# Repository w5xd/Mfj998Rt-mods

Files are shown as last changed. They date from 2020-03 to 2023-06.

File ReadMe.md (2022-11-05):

<h1>MFJ998 tuner modifications.</h1>

Read <a href="LICENSE">LICENSE</a>.

Applying this modification <i><b>CAN</b></i> and <i><b>WILL</b></i> void the
manufacturer's warranty. It introduces risks to itself and your antenna and transmitter beyond those in the manufacturer's
firmware. Use of this PCB and sketch <i><b>CAN</b></i> and <i><b>WILL</b></i> 
damage any and all of these:
<ul>
<li>The MFJ998 tuner itself and components in it.
<li>Any coax cables connected to this tuner's input and/or outputs.
<li>Any antennas connected via those cables.
<li>Any transmitting and/or amplifier equipment connected to those cables.
</ul>

<h2>The Story</h2>
This project's origins can be traced back a couple years when lightning 
rendered my MFJ998RT inoperative, taking me off of 160 meters. I have lots
of experience with lightning damaging my equipment and I know its almost aways
a waste of time to try to repair it. I ordered a replacement tuner and put the dead 
one on my work bench. Eventually I took off the cover. And it occurred to me
that all the "big" parts, the relays, the inductors and capacitors, were 
probably not damaged by lighting. MFJ publishes the circuit diagram on their
website, so I started out by noticing the 5V regulator had exploded and went
from there. 
After many months
of working on it part time, I replaced one more IC (the main PIC18 uProc was the last one) and
it came up! Its as good as new. Here is the pile of dead semiconductors that
came off the lightning-struck board.
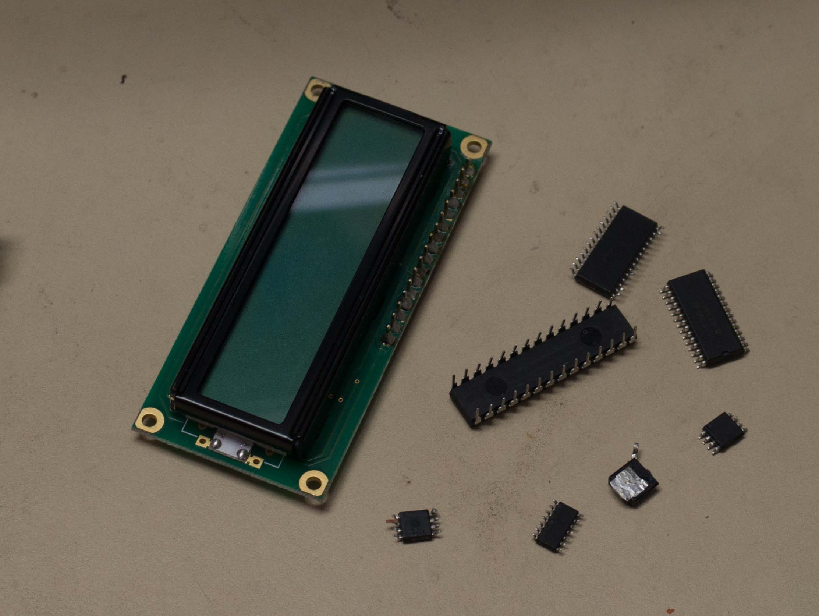
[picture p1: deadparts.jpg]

Now that I know something about how the tuner works, maybe I can improve it for my own
use?

<p>Why replace the as-designed PIC microprocessor?</p>

In contesting scenarios, I found I could not always get the MFJ998RT
to quickly tune to match at the frequency I wanted, and having to
put a low power signal to it to force the tune causes QRM
and takes time. This project adds a <a href='https://learn.sparkfun.com/tutorials/rfm69hcw-hookup-guide'>RFM69HCW 915MHz Wireless Transceiver</a> 
with a maximum range of 500m. It allows direct telemetry of the
tuner's state in both directions from the main operating shack. The
tuner, for example, can be commanded to set itself to an operating
frequency without sending any RF down its coax.

<p>Design rationale</p>

I chose the Arduino for the daughterboard because it is
inexpensive, I am familiar with the development environment, and
its pinout is more than enough to replace all the necessary
functions for the remote version of the tuner. 

<h2>Installation</h2>
<ol>
<li>Remove the weatherproof cover. 
<li>Remove the shield that covers the PIC18 uProc.
That shield has three #6 machine screws, each with a locknut, three #4 machine screws,
each with a locknut, and a #6 nut.
<li>Carefully pry the 28 pin PIC18 IC out of its socket. This is a "no holes" modification, so save the IC and you can restore factory operation by replacing it.
<li>Install this daughterboard as shown in the photo. Caution: it is possible to be
off-by-one row when pressing the daughterboard's header into the 28 pin socket. 
Use a flashlight and peer underneath before you apply power! 
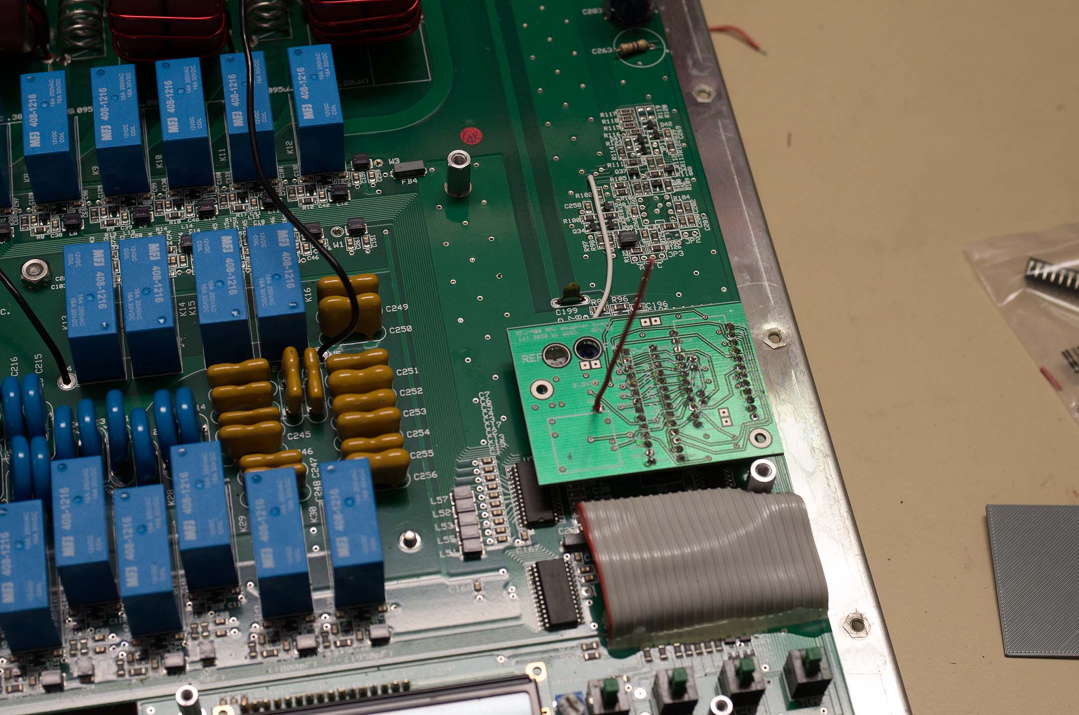
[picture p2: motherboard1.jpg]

<li>The tranceiver's antenna must extend straight up, at a right angle to the PCB. Don't worry about how it will get through the shield. There already is a hole for it.
<li>Place the 3D printed spacer part over the PCB. Its purpose is to insulate the
PCB traces from the shield.
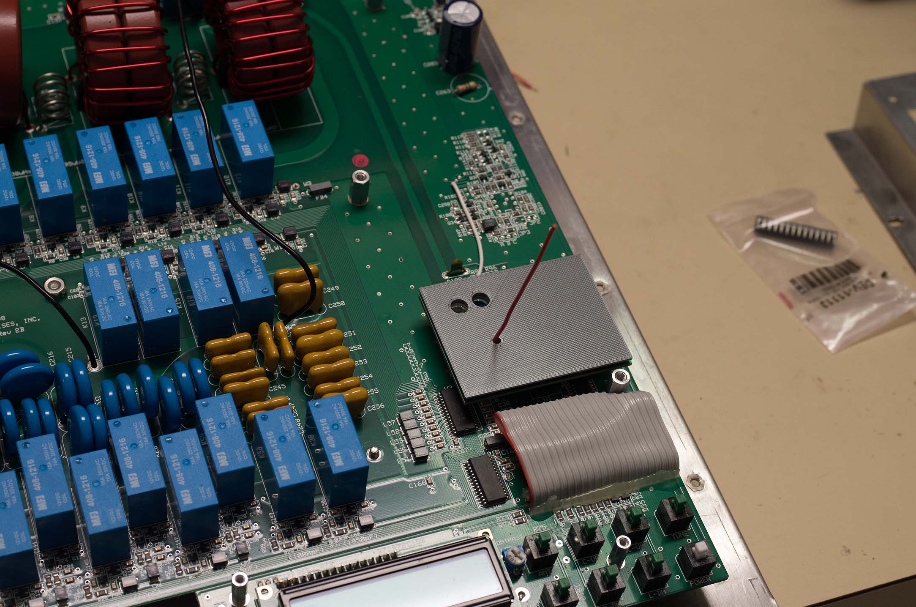
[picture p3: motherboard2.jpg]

<li>Put the unit back together, first the shield and then the weatherproof cover.
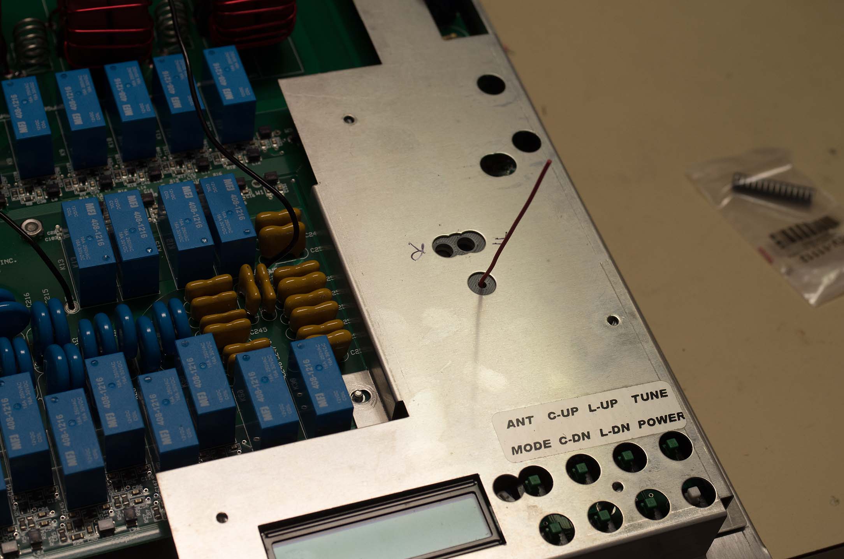
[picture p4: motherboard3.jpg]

</ol>

<h2>Operation</h2>
The daughterboard sketch has some primitive functions available on the push button panel and LCD display,
but its primary purpose is to be controlled from the shack PC. <a href='Mfj998Desktop/Mfj998Desktop'>Here</a> is the source code to a Windows application.

<h2>Construction</h2>
The surface mount components, minus the RFM69 transceiver, are
installed first. Hints for reflow soldering: the gerber file solder paste mask thinks you're going to reflow
 solder the RFM69, but it's probably safer to hand solder. Its your choice. I put a tab of masking tape over its holes in my
solder paste mask. Also, the Revision 2 solder paste mask omits the mask holes necessary for C1, C2, and C3, so I hand-applied more paste after pulling the mask off.
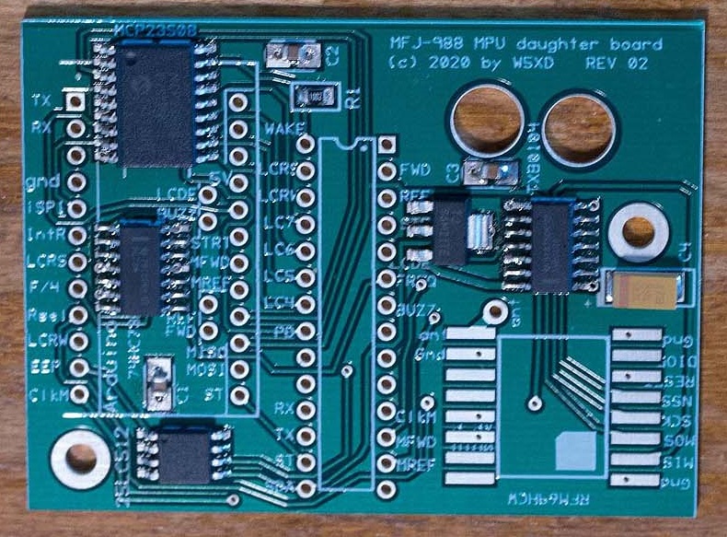
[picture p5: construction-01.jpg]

Install <b><i>only</i></b> the headers at the PIC position
and the Arduino position. There are several incorrect orientations
possible! It is impossible to fix a soldered-in header in the
wrong orientation. The header pins go into the board from the 
same side the SMDs are mounted, and the <i>short</i> header pins 
solder into the board. The bottom side of the board, then,
has nothing on it, and the short pins of the headers protruding.
 Here are step by step pictures. Use a jig of some sort to keep the headers at right angles to the PCB. I started with the ones for the PIC position.
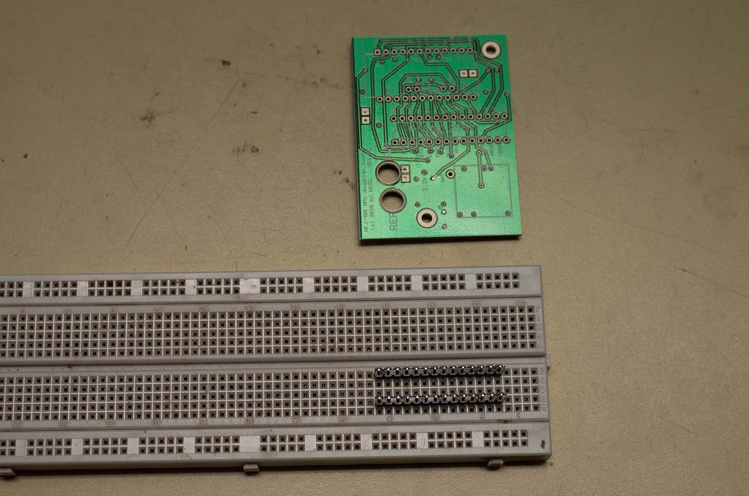
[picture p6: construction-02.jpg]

Check the PCB and header pin orientation. This is your last chance. Solder the PIC headers. 
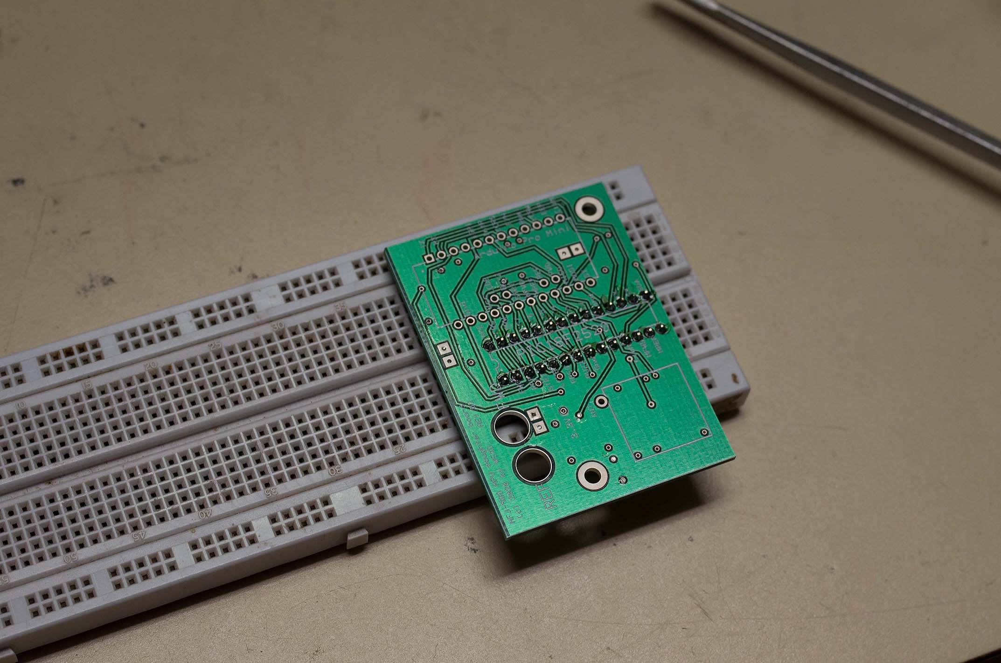
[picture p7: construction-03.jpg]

My jig won't accommodate both the Arduino and PIC headers, so I improvised. Only one row of
Arduino headers at a time.
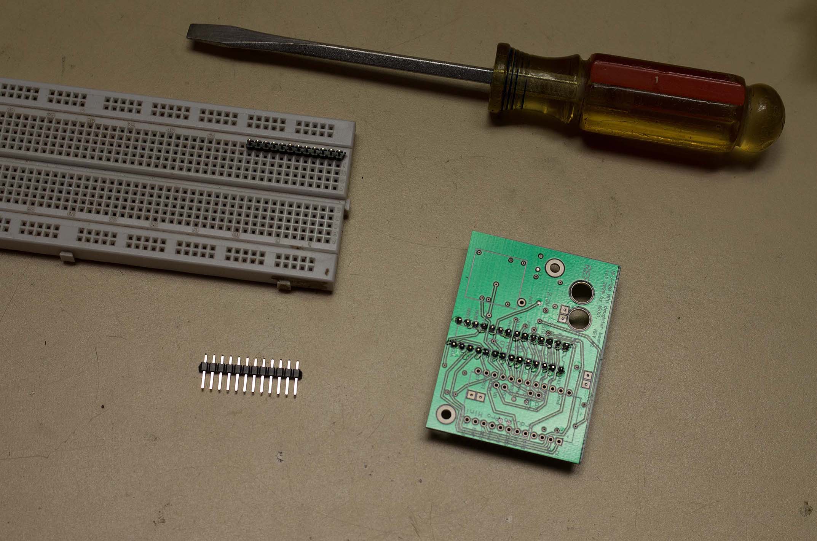
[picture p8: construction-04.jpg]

The first Ardunio header is soldered in while maintaining a right angle.
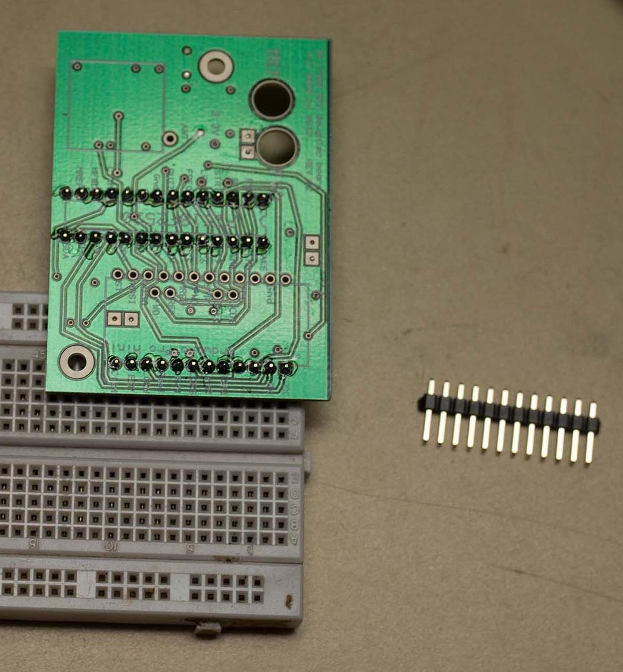
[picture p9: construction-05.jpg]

I used the Arduino as a jig to hold the headers for soldering its remaining headers.
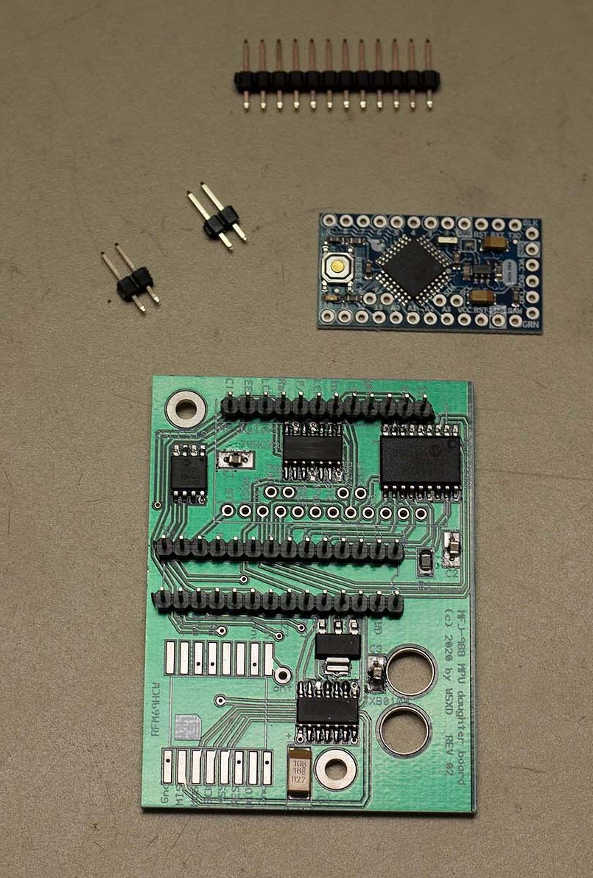
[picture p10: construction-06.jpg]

No soldering is done at this step! Now flip the PCB over without losing the loose Arduino nor its headers.
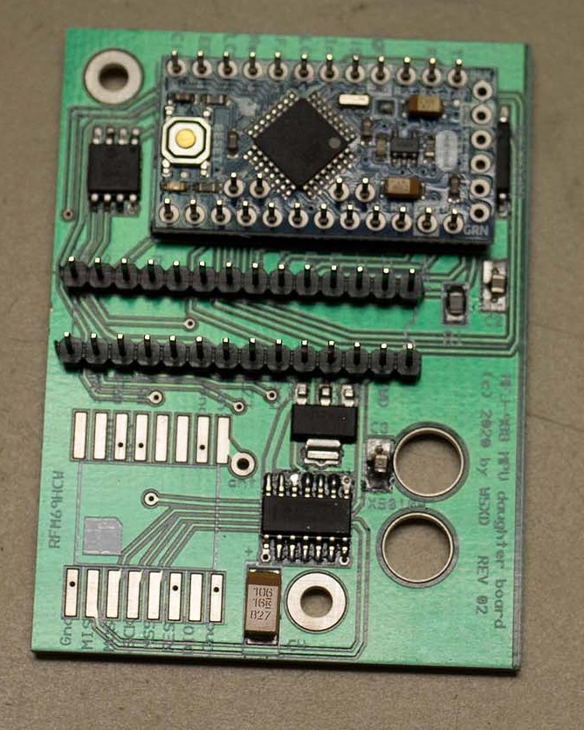
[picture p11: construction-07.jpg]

The Arduino drops down to the work surface, but the soldering happens on what is now the top of the PCB.
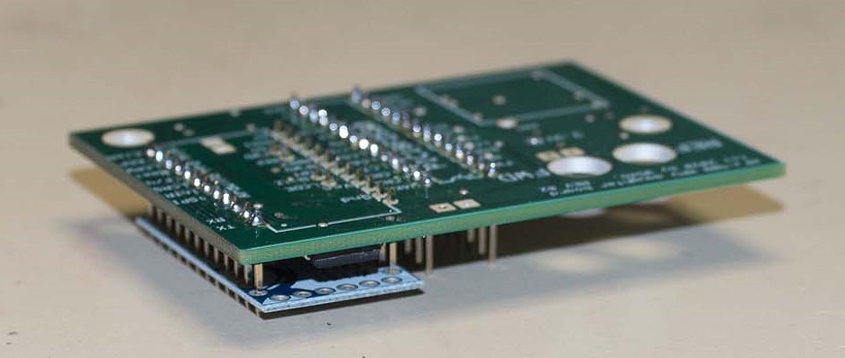
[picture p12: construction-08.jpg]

I only soldered one or two pins on each of the three headers so I could take a peek at the other side before committing all the pins. Then finish soldering all the Aruduino headers to the PCB (the ones you can see in the photo below), but do not solder in the Arduino yet!
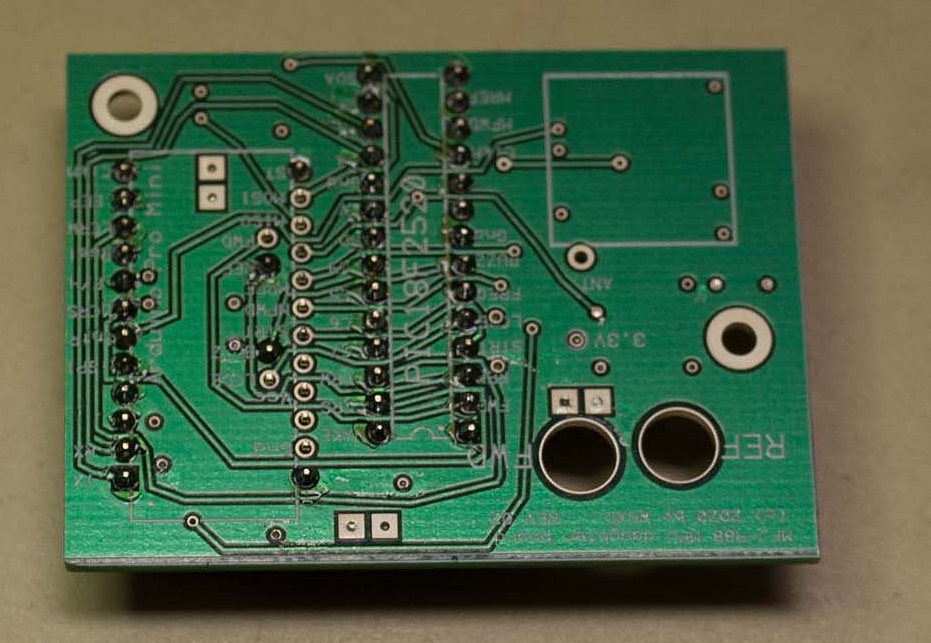
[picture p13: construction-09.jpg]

<h3>Test now. Do not finish assembly</h3>
Its time to try TestHarnessSketch running on my Mega. There are a lot of jumpers required.
See the details in <a href='TestHarnessSketch/TestHarnessSketch.ino'>TestHarnessSketch.ino</a>.
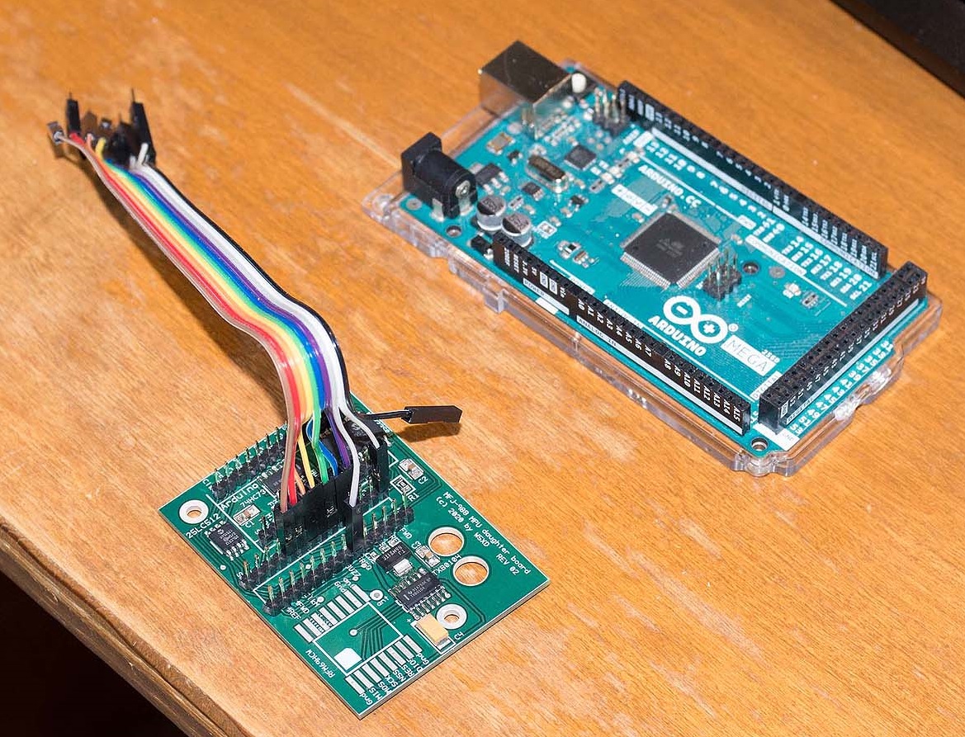
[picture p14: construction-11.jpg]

I used two ribbon cable 10 pin male-to-female jumpers, one for all the PIC header jumpers (shown above) and another 
for all those to the Arduino header jumpers.
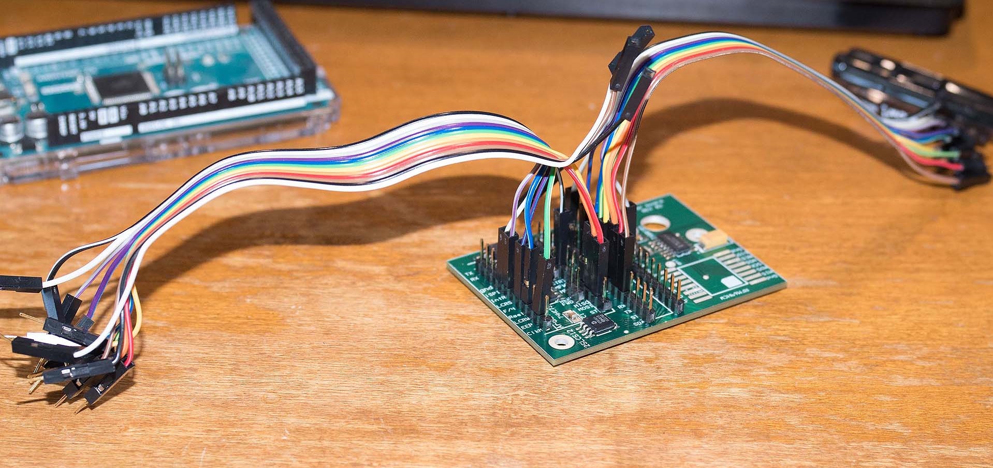
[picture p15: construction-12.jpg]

Plug each of the jumpers where it belongs in the Mega. Again, see the sketch at <a href='TestHarnessSketch/TestHarnessSketch.ino'>TestHarnessSketch.ino</a> to see which jumper connects to which pin..
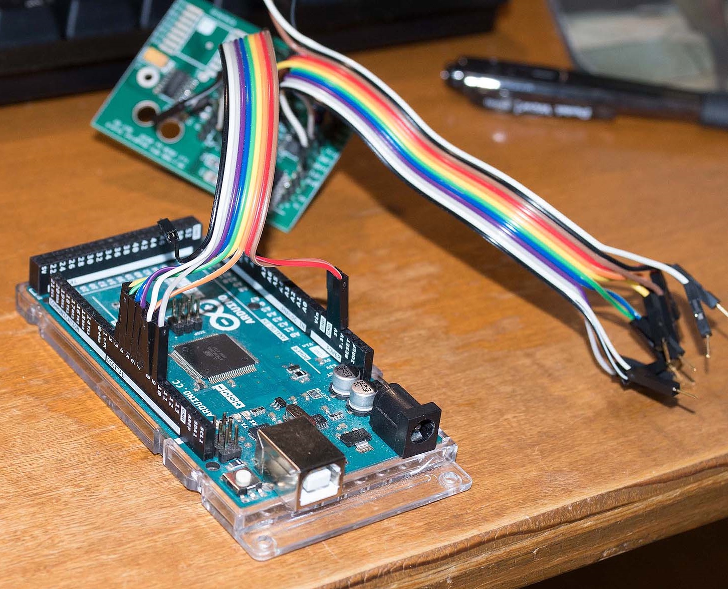
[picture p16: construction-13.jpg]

Finally, all the jumpers for both sets of headers.
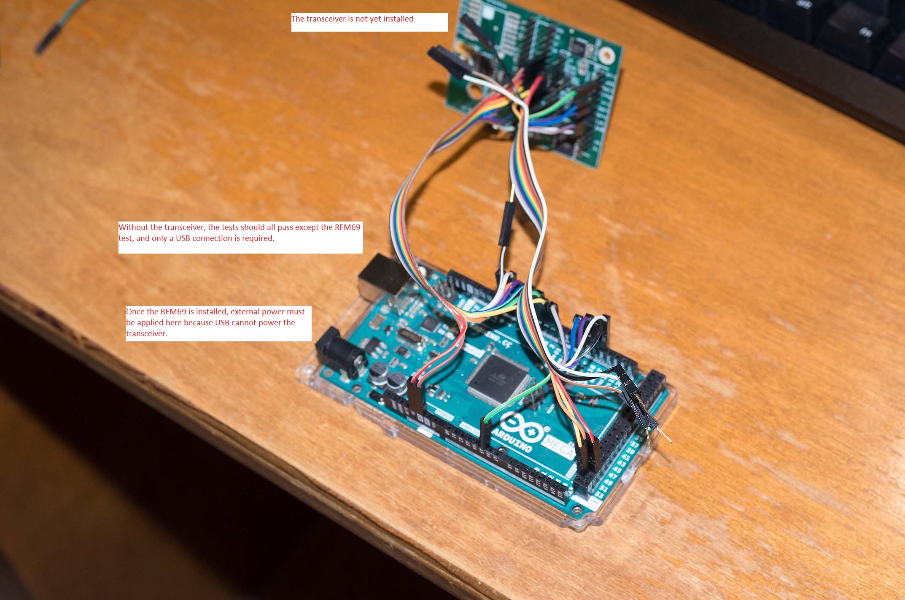
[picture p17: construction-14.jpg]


With only the SMD components installed (minus the RFM69, which
cannot go in the reflow oven) use jumper wires between the
partially assembled daughterboard with no arduino, and not
plugged into the MFJ998 motherboard. See the TestHarnessSketch
for detailed instructions for the jumpers. Only the RFM69 test
fails. If anything else fails, this is your last chance to
fix the SMD soldering!

<blockquote>
<code>
<pre>
All Tests
EEPROM write to address 0 and 0xfff0
EEPROM read from address 0 and 0xfff0
EEPROM write other values to address 0 and 0xfff0
EEPROM read from addresses
Init FREQ_DIV4 counter
FREQ_DIV4 counter high OK
FREQ_DIV4 input low OK
Got F/4
MSCP23S08 registers
   0x0 =0xFF
   0x1 =0x0
   0x2 =0xC0
   0x3 =0x80
   0x4 =0xC0
   0x5 =0x8
   0x6 =0xBF
   0x7 =0x40
   0x8 =0xFF
   0x9 =0xBF
LCD bits set to 0x1. LCD4 OK LCD5 OK LCD6 OK LCD7 OK
LCD bits set to 0x2. LCD4 OK LCD5 OK LCD6 OK LCD7 OK
LCD bits set to 0x4. LCD4 OK LCD5 OK LCD6 OK LCD7 OK
LCD bits set to 0x8. LCD4 OK LCD5 OK LCD6 OK LCD7 OK
Initial iSPI is OK (high)
Read pins 0xbf correct (PD is only low input)
extender WAKEUP_PIN OK (went low)
WAKEUP_PIN is in interrupt mask. OK
extender removed iSPI on WAKEUP high, OK
extender PD_PIN HIGH OK
Extender interrupt on PD high, OK
RFM69 TEST FAILED***********************
</pre></code></blockquote>

Solder the RFM69 transceiver into place. Add its antenna per the
the notes <a href='https://learn.sparkfun.com/tutorials/rfm69hcw-hookup-guide'>here</a>. Note that the TestHarnessSketch
likely will no longer run without external power applied to your
Test Machine (a Uno or Mega is recommended). USB-supplied power is
insufficient to power the daughterboard once the RFM69 is in place.

<blockquote><code><pre>
MFJ998 daughter test harness (rev02)
Type A to test All. E to EEPROM, X to test extender, F for frequency divider

All Tests
EEPROM write to address 0 and 0xfff0
EEPROM read from address 0 and 0xfff0
EEPROM write other values to address 0 and 0xfff0
EEPROM read from addresses
Init FREQ_DIV4 counter
FREQ_DIV4 counter high OK
FREQ_DIV4 input low OK
Got F/4
MSCP23S08 registers
   0x0 =0xFF
   0x1 =0x0
   0x2 =0xC0
   0x3 =0x80
   0x4 =0xC0
   0x5 =0x8
   0x6 =0xBF
   0x7 =0x40
   0x8 =0xFF
   0x9 =0xBF
LCD bits set to 0x1. LCD4 OK LCD5 OK LCD6 OK LCD7 OK
LCD bits set to 0x2. LCD4 OK LCD5 OK LCD6 OK LCD7 OK
LCD bits set to 0x4. LCD4 OK LCD5 OK LCD6 OK LCD7 OK
LCD bits set to 0x8. LCD4 OK LCD5 OK LCD6 OK LCD7 OK
Initial iSPI is OK (high)
Read pins 0xbf correct (PD is only low input)
extender WAKEUP_PIN OK (went low)
WAKEUP_PIN is in interrupt mask. OK
extender removed iSPI on WAKEUP high, OK
extender PD_PIN HIGH OK
Extender interrupt on PD high, OK
RFM69 test passed
All tests passed
</pre></code></blockquote>
<h3>Finish assembling</h3>
Now its OK to solder in the Arduino. Install a right angle header on the 6 pin side of the Arduio Pro Mini. See the photo for the required orientation. This header is used
to program the device.
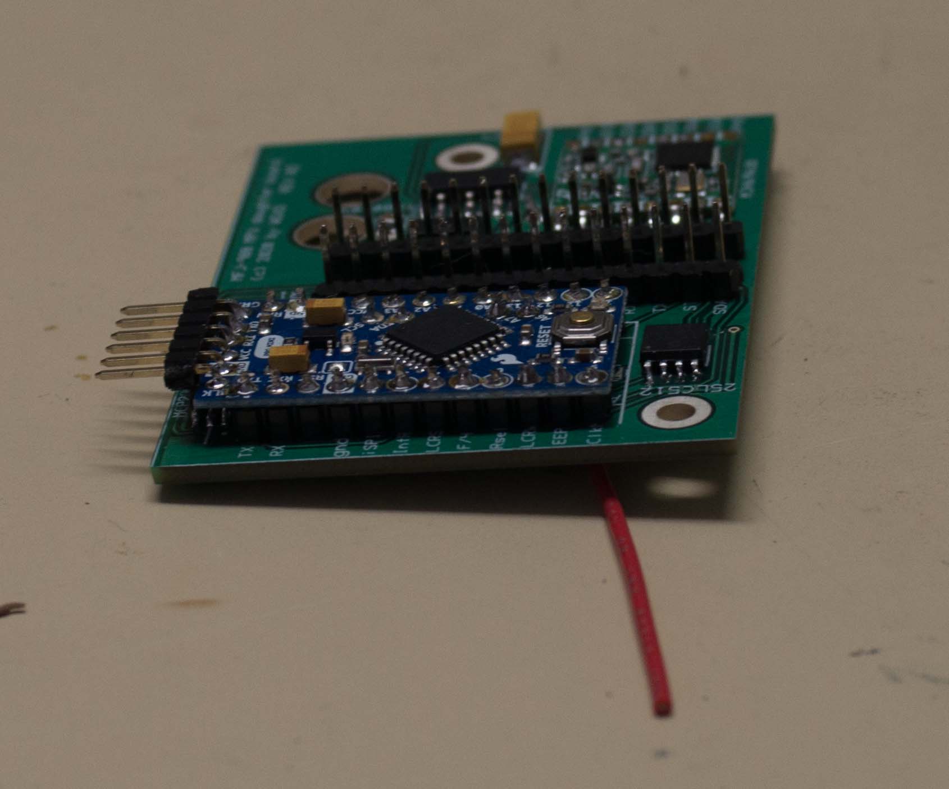
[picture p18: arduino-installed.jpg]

The red wire is the transceiver's antenna.

<h2>Install the sketch software</h2>
Use the Arduino IDE to install mfj998sketch. The daughterboard must not be 
plugged into the motherboard to program it through its 6-pin header. 

Note: the Arduino serial port
is routed through the daughterboard to the MFJ998's back panel serial connector, but without the DTR pin
that the Arduino IDE uses to reset the device at programming time. The
Arduino can be programmed as installed in the motherboard using a serial cable
to the MFJ998's back panel using careful timing of the power switch and 
the Arduino "upload" button. See the Arduino documentation.
 
<h3>CAD</h3>
The CAD and STL directories contain the 3D designs of a couple
of plastic parts that might be useful.

<p>Mfj998rtTerminalCover.STL</p>
In my installation, the antenna is a wire connected to the tuner's
wire terminal input, and the tuner is mounted with that hole facing
up, and therefore with rainfall exposure. When not in use, I move
the antenna wire to the adjacent grounded wingnut and pop this
plastic part to offer better weather protection to the wire terminal.

<p>Mfj998LcdSpacer2.STL</p>
Lightning destroyed the LCD in my MFJ998RT. I found the manufacturer's
soldered-in header extremely difficult to remove with the dead part.
To install the new device, I did not use a header but instead soldered
12 individual two inch long AWG 24 solid insulated wires for pins 1-6
and 11-16. Pins 7-10 are not used in the original. That resulted in an LCD
that can be uninstalled relatively easily, but is not held in place
securely. Print the part above and it properly frames the LCD in the 
window in the aluminum shield.

<h3>MFJ998RT versus the MFJ998 indoor version.</h3>

While the main PCB on the MFJ998RT is nearly identical to the indoor version
of the tuner, the MFJ998, and the daughterboard could obviously be
plugged into that indoor version, this sketch does not support 
everything needed for the indoor version's operation. The PCB
hardware connects all the same signals to the Arduino that were
available to the original PIC processor, so maybe you can modify
this code to be useful on the indoor model.

MFWD and MREF are routed to the Arduino, but are not supported by this sketch.
The START line is also routed (it comes from the PIC band selector uProc
on the motherboard) but 
is not supported in the sketch published here. The communication protocol for that PIC uProc is
not, as far as I know, published by MFJ.

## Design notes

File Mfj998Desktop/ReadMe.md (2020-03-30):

<h1>MFJ998Rt tuner Desktop control</h1>

Read <a href="../LICENSE">LICENSE</a>.

This is a Windows .NET application that interfaces with an MFJ998RT tuner modified per the
the details <a href="https://github.com/w5xd/Mfj998Rt-mods">here</a>. That modification replaces the controller microprocessor
in the tuner and the result is a tuner with a very different set of features than the 
original, and a very different way of operating.

Calibration

This MFJ998 Desktop application is designed to be set up (or "calibrated") starting with
antenna analyzer data acquired at the point where the tuner will be installed. From that data this application
uses formulas to calculate the necessary inductance and capacitance to transform the
antenna impedance to 50 ohms resistive. (What formula? See the function fromRXf in DesktopForm.cs. Where
did that formula come from? See introductory electrical engineering texts on linear circuit theory for
calculating complex impedances.) In addition to requiring the complex impedances, this application requires
you to make a choice, for each frequency band, of how many segments to divide that frequency band for storing
the calculated L and C values. An antenna with steep changes in impedance over frequency needs more segments
than one that varies slowly. This Desktop application and the daughterboard firmware enable loading the
Ls and Cs and number of segments into the tuner using the 9 pin COM port connector on the tuner and cabled
to the PC running this application. That is, the initial part of the tuner setup requires its weatherproof cover
removed and a serial cable running between the desktop and the tuner. The L and C values loaded at this time
can be updated later using the UHF transceiver, however the number of segments cannot be changed except
via the serial cable.

Caveat: I have found this technique of calculating the tuner's L and C settings from analyzer data to work
reliably only up to about 7MHz. For the 40m band and above, and for my own antenna, I have found it necessary
to use L and C settings in the tuner nowhere near those calculated using this technique. This desktop application
has the capability to do the necessary tweaking over the UHF link. (Why does the calculation fail? My guess is
that the tuner itself cannot be reliably modeled as a simple series inductor with capacitor to ground at 
higher frequencies.)

Step by Step

Start with an antenna analyzer at the point where the tuner will eventually be installed. Use it to measure
the complex input impedance over the frequency ranges that you plan to operate, and create a file. The frequency
range in the file can be any that is convenient. I recommend a separate file per amateur band. The
Desktop application expects to read the real part (in ohms) and the complex part (in ohms) in either a .CSV
file (comma separated values) or a .ASD file (XML analyzer file.) With those files available, start this
MFJ998 Desktop application. 

Use this application's "Select analyzer data" button to read in one of the files. If necessary, adjust the min 
and the max frequency selectors to cover the band you want to load into the tuner. The application presents
a (very arbitrary) default selection of 50 segments for the band. You'll likely need to experiment with this,
but my experience is that 50 is high number and fewer segments work OK, and leaves less tweaking to do over the
radio link later.

Adjust the number of smoothing points to deal with the fact that the analyzer data is somewhat noisy. The application
updates its graphs as you make the changes. The three graphs show, top to bottom: <ul>
  <li>The measured complex impedance as R and X (real and imaginary parts in ohms.)</li>
  <li> The calculated series inductance required, in units of uH</li>
      <li>The calculated parallel capacitance required in units of pF. And the symbol for the capacitance graph indicates 
        whether the capacitance is required on the load side of the tuner (or antenna side) or on the generator side 
        (or transmitter side.) </li>
</ul>

With a serial cable (3 conductors are requred: TXD, RXD and ground, the other 6 are unused) connected between the tuner
and this desktop, use the "Tuner port" selector to choose the port on the PC that is connected to the tuner. The "Clear tuner 
memory" button clears out <b><i>all</i></b> L and C settings in the tuner! Use the "To MFJ998" button to replace the
tuner's settings only for the frequency range selected by min and max. Settings already in the tuner for other frequencies
are unchanged. (The tuner firmware's behavior if you try to give it overlapping min/max settings is undefined. I haven't 
tested it, but it won't work predictably.)

Repeat the process of loading analyzer data, setting the number of segments and smoothing, and "To MFJ998" for each band
that you will want to support.

Disconnect the serial cable. Relocate the tuner to the antenna feedpoint and connect a coax with 12VDC on its center 
conductor using MFJ's instructions for how to feed power to the tuner. Use the "Gateway port" selector and choose
the COM port corresponding to the Arduino running the <a href='../GatewaySketch'>GatewaySketch</a>. This desktop application (currently) can only talk to one modified MFJ998RT at 
a time, and that tuner's daughterboard must have been setup for the same frequency and at the Node ID you select here.
Once those two are set correctly in this application and while the tuner has 12VDC applied, the application will show
the text of the messages the two are exchanging.

The Trigger and Stop settings initially show how the tuner's daughterboard's EEPROM is set. Click Restart to refresh
this display. Trigger is the SWR value that causes the tuner firmware to start a search, starting with its programmed L/C
settings for the frequency it sees from your transmitter. Stop is the value that, if it finds an L/C with an SWR
of this or better, it stops searching.

The desktop's C, L and P selectors use the UHF link to override the values the tuner daughterboard has chosen.
The "P" value is zero or one, which correspond, respectively, to the capacitance on the load (antenna) side, or the generator
(transmitter) side.

The Set EEPROM button commands the tuner, over its UHF link, to overwrite its EEPROM setting just for the segment corresponding
to the current frequency it has acquired (as displayed here) and with the L, C and P values displayed.

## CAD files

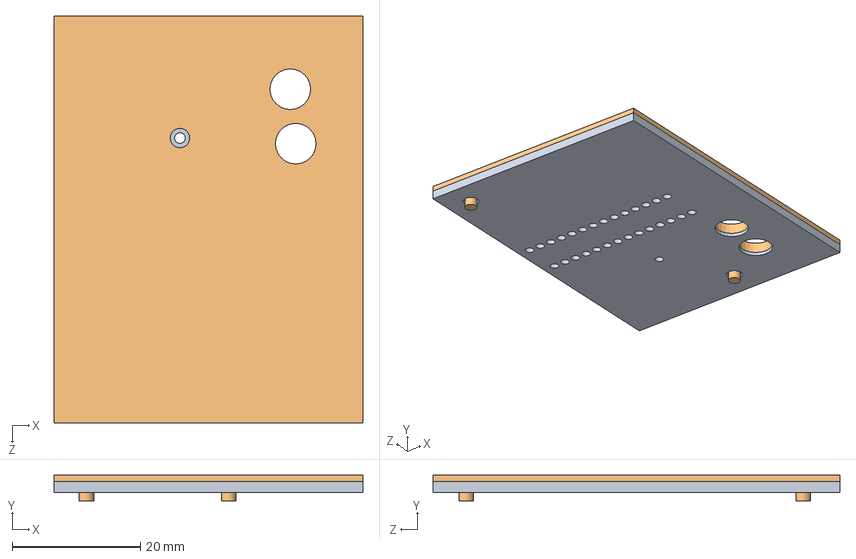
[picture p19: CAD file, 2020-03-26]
CAD/Mfj998-db.SLDASM
48.3 x 4.00 x 63.5 mm
Mfj998DaughterboardPCBmodel
Mfj998DaughterboardPCBspacer

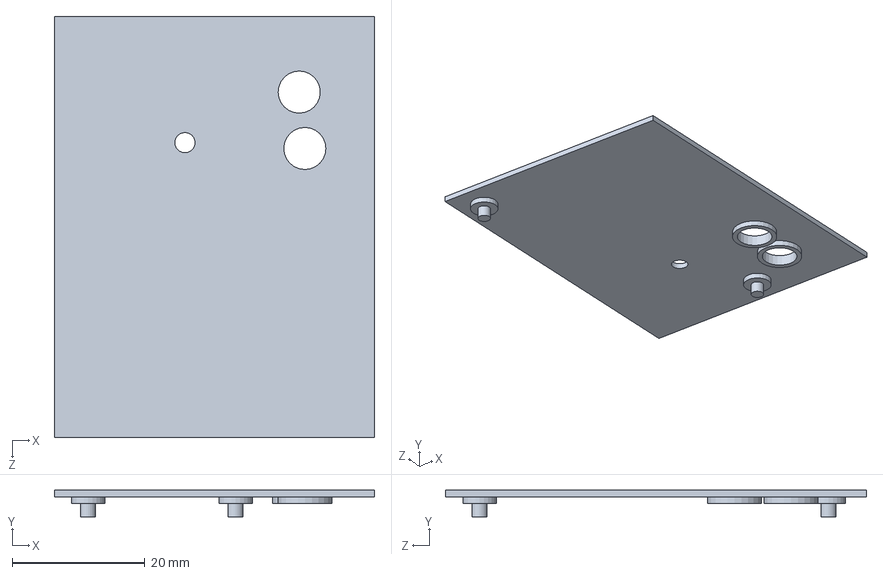
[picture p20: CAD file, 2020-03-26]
CAD/Mfj998DaughterboardPCBspacer.SLDPRT
48.3 x 4.00 x 63.5 mm

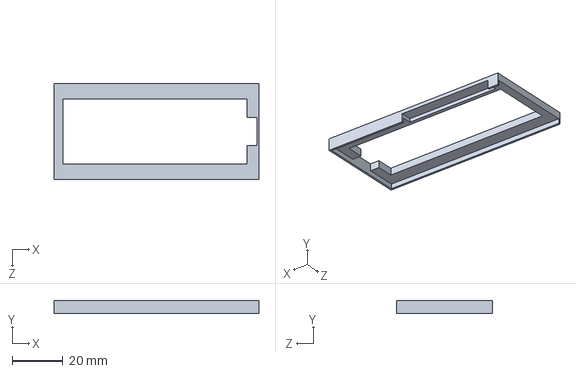
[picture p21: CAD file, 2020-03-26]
CAD/Mfj998LcdSpacer2.SLDPRT
80.8 x 5.00 x 38.0 mm

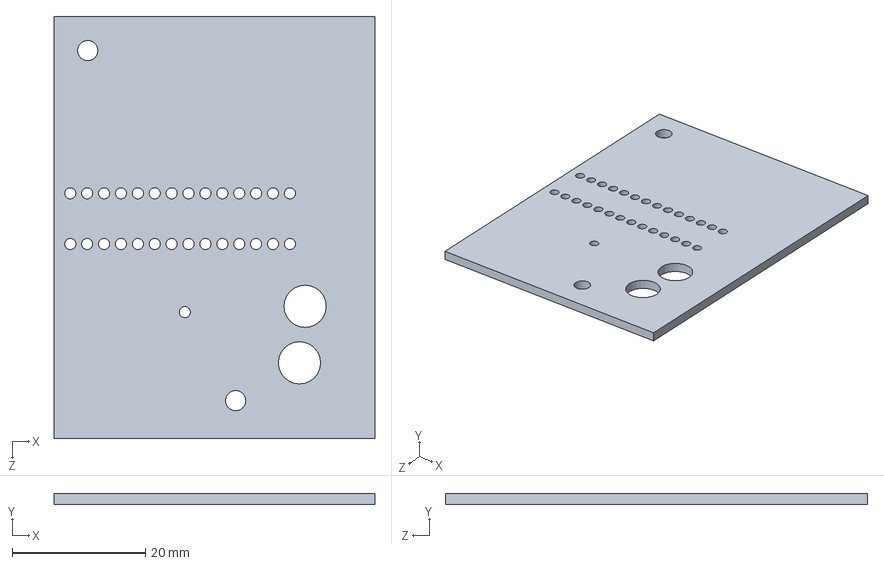
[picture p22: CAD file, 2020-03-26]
CAD/Mfj998DaughterboardPCBmodel.SLDPRT
48.3 x 1.70 x 63.5 mm

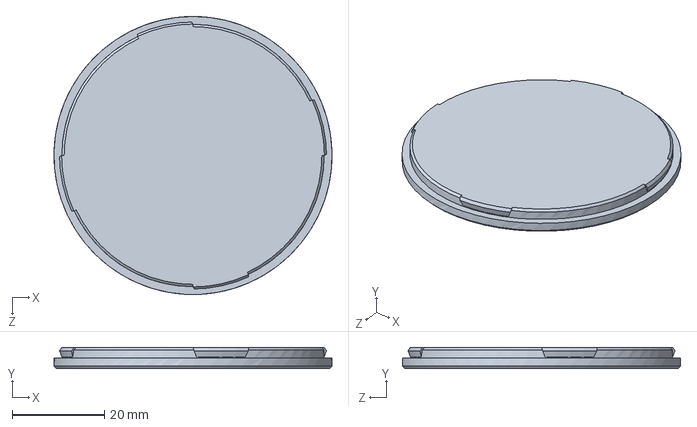
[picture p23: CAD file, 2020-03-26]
CAD/Mfj998rtTerminalCover.SLDPRT
60.3 x 4.57 x 60.3 mm

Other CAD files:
STL/Mfj998DaughterboardPCBspacer.STL
STL/Mfj998LcdSpacer2.STL
STL/Mfj998rtTerminalCover.STL

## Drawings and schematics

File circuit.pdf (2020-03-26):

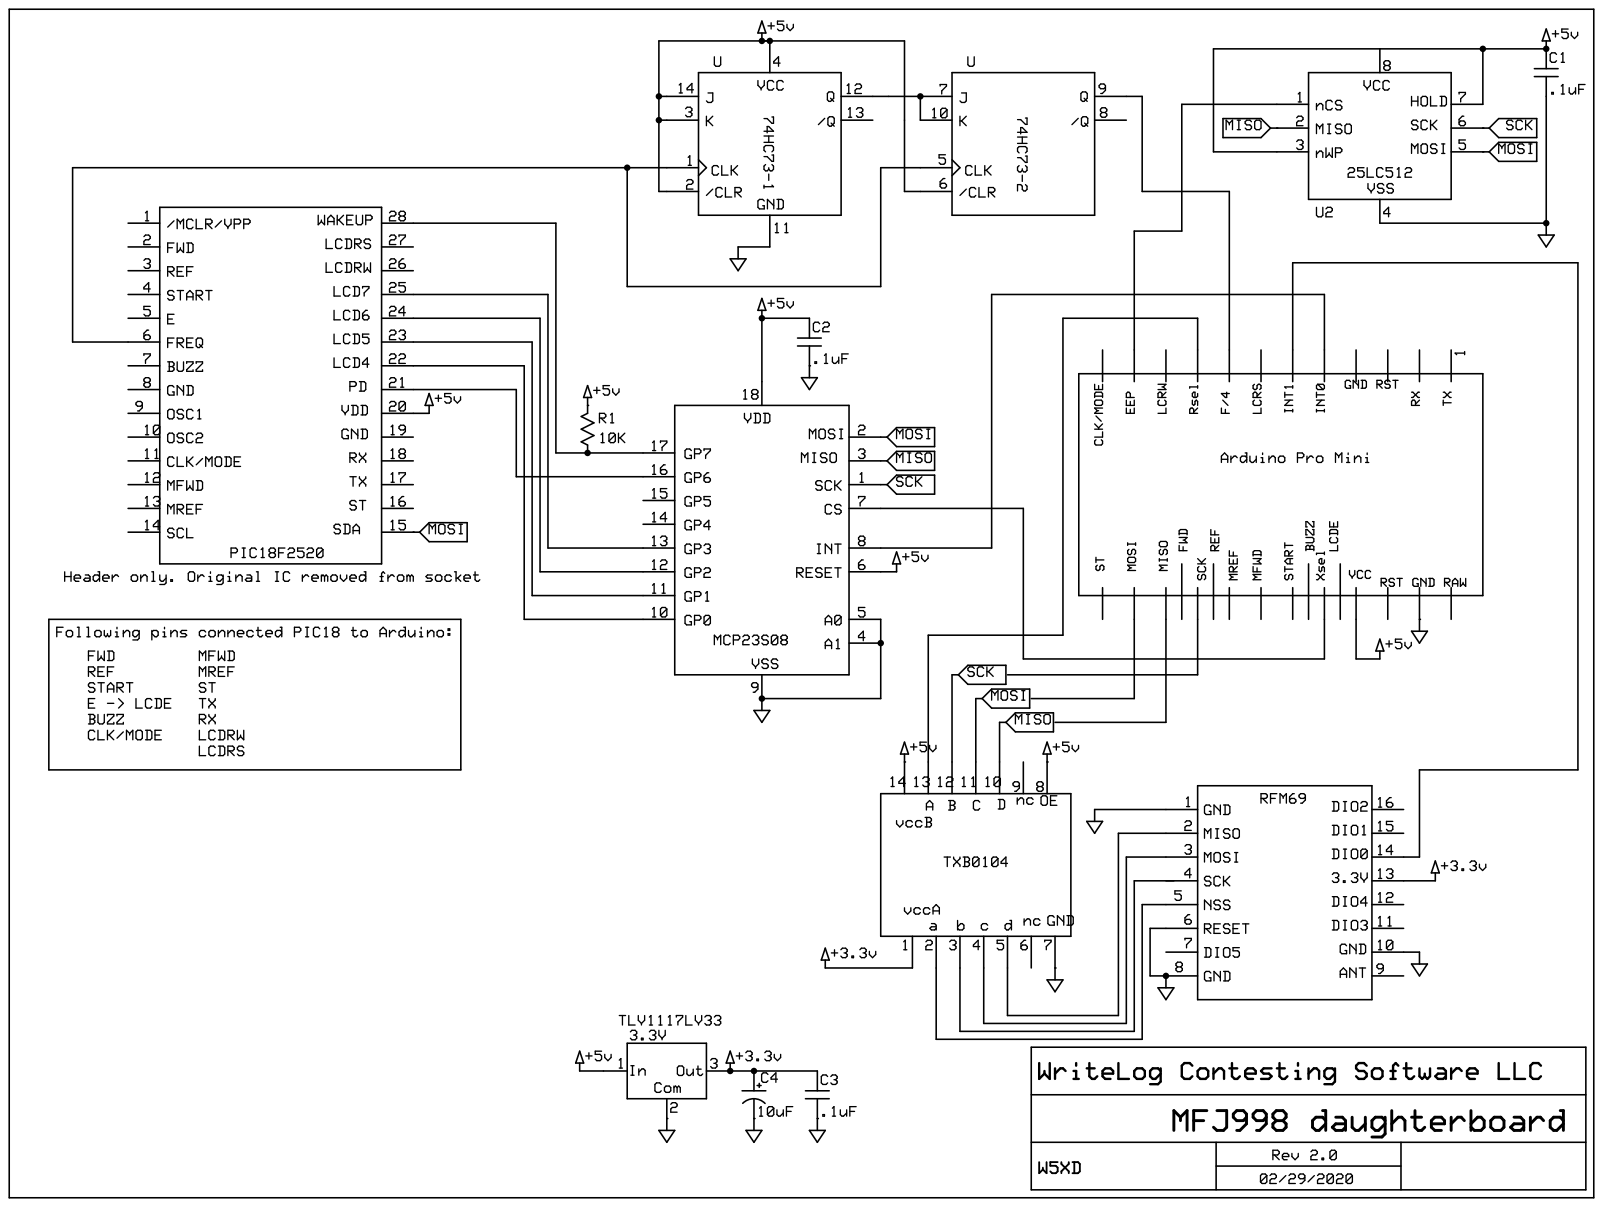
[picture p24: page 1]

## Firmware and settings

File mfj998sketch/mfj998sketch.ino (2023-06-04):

/* mfj998sketch
** Copyright (C) 2020 by Wayne Wright, W5XD. All rights reserved
**
** for REVISION 2 of the PCB
**
** This sketch is for a daughterboard (designed published in this
** same archive) plugged into the socket for U1 on the MFJ998 antenna tuner. 
** The processor on the daughterboard is an Arduino Pro Mini, which
** has an Atmega328 CPU.
**
** Why replace the manufacturer's PIC microprocessor?
**
** The daughterboard adds a RFM69HCW Wireless Transceiver for 915MHz
** with a maximum range of 500m. This allows telemetry of the
** tuner's state in both directions with the main operating shack.
**
** This sketch (currently) does not duplicate the entire feature set
** in the original firmware. Instead, its main purpose is to enable
** control of the tuner over a 900MHz radio from the shack rather than 
** indirectly through the tuner firmware's supported process of putting a 
** low level RF signal on the line in order to get the tuner to tune.
**
** What the daughterboard does and how to use it.
** On detecting this combination of circumstances:
** 1. power level has sampled in this range: 5W and 25W for
**  MSEC_OF_TUNE_POWER_TO_ENABLE_SEARCH consecutive msec (500) or longer
** 2. frequency detection has been in the range of its
** indexed EEPROM table.
** 3. if an SWR higher than "trigger SWR" is detected, it
**  decides whether to move its L and/or C based on:
**  If it has done an SWR search (defined below) since its
**  last powerup on a previous frequency in the range of
**  +/- 1/32 (FREQ_DELTA_FRACTION_PWR) of the current frequency, then it does nothing.
**  (you have to power it down and back up, or else QSY to
**  get it to change.)
**  4. It looks up the EEPROM stored L/C for the current frequency.
**  and puts the L/C to that table entry.
**
** All of the signals on the original PIC that remain useful are
** routed somewhere on the daughterboard and are available to this
** sketch. NOT all of them are used or supported (currently).
**
** Peripherals and daughterboard wiring
** (A) on the MFJ998 motherboard                             total on Atmega328
**     1. LCD display (7 pins, but 4 are on MCP23s08 extender)  3
**     2. WAKEUP (routed through port extender)                 4
**     3. Serial port (2 pins)                                  6 
**          (The arduino Serial appears on the tuner's back panel DB9.)
**     4. Buzzer                                                7
**     5. FREQ (RF as sniffed and made digital in schmidt trig) 8 
**     6. FWD/REV analog inputs  (2 pins)                       10
**     7. U3/U4 relay latches. (3 pins, including MOSI)         13
**     8. MFWD/MREV (PWM front panel meter outputs)             15
**     9. U2 rig controller START (but no support in sketch)    16
**     Front panel switches (6 shared with LCD)
**  (B) NOT routed from MFJ998 motherboard to daughter MPU
**     x EEPROM i2c SCL on motherboard (EEPROM on mainboard untouched)
**  (C) used pins internal to the daughterboard
**       SPI is 3 pins, but MOSI is shared with above           18
**     1. RFM69 transceiver (2 dedicated + SPI)                 20
**     2. 512KB SPI EEPROM    (1 dedicated + SPI)               21
**     3. CS on MC23S08 port extender                           22
**  (D) pins on MC23S08 port extender                          total on extender
**     1. 4 LCD pins D4 through D7                               4
**     2. PD (power down)                                        5
**     3. WAKEUP (input on extender, and INT output)             6
** 
** Arduino Pro Mini has 22 I/O pins total...all are used.
** The port extender has two unused pins.
**
** 900MHz GATEWAY
** This source archive has a GatewaySketch that implements the
** shack end of the 900MHz link, also requiring the RFM69 board.
**
** Test Harness.
** The daughterboard itself has headers for smaller break-out boards. 
** The Pro Mini board in particular has the constraint that it
** is mounted over SMD ICs. Without physical space in the tuner
** cabinet to allow for sockets, the Pro Mini has to be soldered
** in place. Do NOT solder the Pro Mini in place without following
** the instructions for using the Test Harness sketch on another
** Arduino board (like a Uno or Mega) to check your soldering of 
** the SMD ICs. 
**
** HARDWARE DETAILS
**
** The code in this sketch is a mix of use of standard Arduino libraries
** (e.g. SPI and pinMode, and digitalRead) and sections specific to the
** the Pro Mini hardware ATmega328P. The result is a sketch that,
** on the whole, can only run on the daughterboard as built on the PCB
** in this repo.
**
** For almost all the pins and controls on the MFJ998, the function
** and design intent is obvious. However, there are three that this author, 
** for full disclosure, is not so sure of:
**
** PD
** Its obviously an abbreviation for "power down" and an oscilloscope
** shows that the CPU gets about 15msec of operation after 12VDC 
** power is is removed such that the PD signal appears. What's not 
** obvious is what the CPU is supposed to do with those 15msec. Maybe
** it has to do with the EEPROM that stores the antenna settings?
** That EEPROM has data that must be accessible across power cycling, and it has
** a 5msec write cycle. That is, if you start a write cycle that
** is aborted by a power down, then you don't know at power up 
** what you're going to find. 
**
** K1 and its 25 ohm series resistor.
** The relay obviously adds R121, a 25 ohm series resistor, 15W, 
** between the SWR bridge and the matching network. Because its a 
** 15W part, its reasonable to assume its useful only at tuneup time 
** (i.e. opening K1 while 1500W is applied to the tuner would 
** vaporize R121.) It's definitely not for current limiting at
** relay switching time turning tuneup because its on the wrong
** side of the SWR bridge (it affects the measured SWR.) Guess again...
** My best guess: R121 is an aid to determining whether the
** antenna impedance real part is higher or lower than 50 ohms.
** Measure without; then add it in. If it makes things better,
** guess that the real part is below 50 ohms, otherwise above.
** Knowing that real part w.r.t. 50 ohms is useful because it says 
** whether the matching network capacitance belongs on the generator 
** side (real part below 50 ohms) or load side (real part less.)
** However, regardless of these guesses, this sketch has no code to use
** K1/R121.
**
** START
** This pin is used to communicate with another PIC CPU on the MFJ998
** motherboard that, in turn, interfaces to rig hardware. That second
** PIC is not even installed on the MFJ998RT (remote model). The
** author of this sketch has not seen any documentation for how
** that communication is to take place and this pin is not supported
** in this sketch.
**
** EEPROM
** the i2c EEPROM on the MFJ998 board is not accessed (and not even
** wired to the daughterboard.) This sketch therefore cannot change 
** it. That means the daughterboard and the factory PIC CPU
** can be interchanged at will, restoring the factory functionality
** without even having to do a reset-defaults.
**
** This daughterboard has its own EEPROM with the same capacity
** as the one on the main board. 
**
** The Atmega CPU also has (a much smaller) EEPROM accessed using the
** Arduino standard EEPROM library. This sketch stores its radio 
** setup parameters stored there, along with a few other settings.
** That EEPROM is accessed using the arduino <EEPROM.h>. The
** 512K-bit EEPROM on the daughterboard is accessed using a 
** for-this-purpose-only header at <eepromSpi.h>
*/

// standard Arduino libraries
#include <RFM69.h>      // the wireless transceiver
#include <SPI.h>        // Arduino SPI library 
#include <EEPROM.h>     // Arduinio EEPROM library

#include <LiquidCrystal.h> // MODIFIED to make write4bits virtual

#include <avr/sleep.h>  // sketch only really works on AVR ATmega328P
#include <avr/power.h>
/* The __AVR_ATmega328P__ is used below to mark code that is specific to that processor
** Don't take that to mean it might run on other hardware. It won't. */

#include "PinAssignments.h"

/* code shared with the Gateway that is deployed like a standard
** Arduino library, but has no particular use outside this
** sketch and the gateway sketch. */
#include <portExtender.h>
#include <eepromSpi.h>
#include <RadioConfiguration.h>

#define SERIAL_DEBUG 0 // printout and serial commands to aid debugging

/* All of these conditional compiles make the code much harder to read.
** Sorry about that. However...sometimes I was surprised by hardware
** devices that interact poorly. These compile symbols make it relatively
** easy to exclude software support for key devices and see if the 
** remaining ones change their behavior. */
#define USE_LCD 1
#define USE_EXTENDER 0
#define USE_RFM69 1
#define USE_EEPROM 1
#define USE_RELAYS 1
#define COUNT_FREQ_ON_T1 1 // The T1 input is counted using hardware support 
#define DO_PRINT_FREQ 1 // only relavant on COUNT_FREQ_ON_T1 with USE_LCD
#define PRINT_RADIO_RSSI 0 // one board I built has a radio that reports a questionable RSSI
#define EEPROM_TEST_COMMANDS 0

#define USING_SPI ((USE_RFM69 > 0) || (USE_EEPROM > 0) || (USE_LCD > 0) || (USE_EXTENDER > 0))

#include "Mfj998Relays.h" // depends on the above preprocessor definitions

/* Atmega328 timer/counter #0 is not used explicitly in the sketch because the Arduino timer library uses it
** timer/counter #1 is configured in this sketch to count the external T1 pin, for a frequency counter.
** timer/counter #2 is configured in this sketch to software-generate PWM for the FWD/REF meter outputs.
*/ 

namespace constants { 
    enum class FrontPanelButtons  : uint8_t { // seven buttons on the mfj998 front panel
        DISPATCH_NOBUTTON, DISPATCH_TUNE, DISPATCH_LDOWN, DISPATCH_LUP, DISPATCH_CUP,
        DISPATCH_CDOWN, DISPATCH_ANT, DISPATCH_MODE};

    const int LCD_WIDTH = 16; // number of characters on the LCD display hardware
    const uint16_t MAX_FWD_REF_DURING_SWITCHING = 165;  // about 25W  
    const uint16_t MIN_FWD_TO_ENABLE_SEARCH = MAX_FWD_REF_DURING_SWITCHING / 2;
    const uint16_t MIN_TRIGGER_SWR = 4; // which is 1.125:1 at (SWR-1)*64
    const int MSEC_OF_TUNE_POWER_TO_ENABLE_SEARCH = 500;
    const unsigned long INITIAL_AWAKE_MSEC_ON_POWERUP = 10000; // give user a chance to disable sleep
}
using namespace constants;

class FreqOver4 { 
public:// the daughterboard has a JK flipflop that divides the incoming frequency by 4.
    FreqOver4(): calibration(0x8000), startMicroseconds(0){}

    uint16_t getFreqRaw() const;   // units of MHz * 2048 
    uint16_t getFreqKhz() const;
    bool loop();
    void setup();
    void setCalibration(uint16_t v){ if (v != 0xffff) calibration=v;}
    void wakeup();
    void OnOvf();
    void OnCompA();

protected:
    enum {SCALE_POWER = 11}; // 2**11 = 2048
    struct Measurement {
        Measurement():usec(0), count(0){};
        uint16_t usec;  uint16_t count;
    };
    void acquire(unsigned long nowusec, uint16_t count);
    // the frequency measure is empiracly observed to be stable.
    // no need to keep more than one history point.
    Measurement history;
    uint16_t calibration;
    volatile unsigned long startMicroseconds;
    static const unsigned long MIN_USEC_AT_COMPA;
    static const unsigned long MAX_USEC_TO_DECLARE_ZERO;
    static const uint16_t FIRST_STOP_COUNT;
    static const uint16_t SECOND_STOP_COUNT;
};

class Buzzer {// it buzzes if we wiggle its pin (i.e. steady 5V won't sound)
public:
    Buzzer() :buzzing (false) {}

    bool loop()
    {   // using the loop to buzz introduces audible artifacts
        static unsigned long lastbuzz = micros();
        if (buzzing)
        {
            static const int intervalUSEC = 800; // half cycle. 625Hz
            long thisbuzz = micros();
            int diff = (thisbuzz - lastbuzz);
            if (diff >= intervalUSEC)
            {
                static uint8_t state = 0;
                digitalWrite(BUZZ_PIN, state++ == 0 ? HIGH : LOW);
                if (state > 2)
                    state = 0;
                lastbuzz = thisbuzz;
            }
            return true;
        }
        return false;
    }

    void buzz(uint16_t msec)
    {   // this one sounds good compared to what happens with the
        // loop() implementation. but you can't do anything else concurrently.
        buzzing = false;
        pinMode(BUZZ_PIN, OUTPUT);
        // Sets the pitch of the buzz
        static const int intervalUSEC = 1100; 
        uint32_t usecCount = 0;
        uint32_t finish = msec;
        finish *= 1000;
        while (usecCount < finish)
        {
            digitalWrite(BUZZ_PIN, HIGH);
            delayMicroseconds(intervalUSEC);
            digitalWrite(BUZZ_PIN, LOW);
            // duty cycle controls loudness.. and affects pitch
            delayMicroseconds(4*intervalUSEC);
            usecCount += 5 * intervalUSEC;
        } 
        digitalWrite(BUZZ_PIN, LOW);
        pinMode(BUZZ_PIN, INPUT);
    }
    bool isBuzzing() const { return buzzing;}
    operator bool () const { return buzzing;}
    bool operator = (bool v) { 
        buzzing = v; 
        pinMode(BUZZ_PIN, v ? OUTPUT : INPUT);
        return v;}
protected:
    bool buzzing;
};

class RadioRFM69 :  public RFM69, 
    public Print//has easy-to-use formatting routines for our telemetry
{
public:
    RadioRFM69() 
        : RFM69(RFM69_SELECT_PIN, RFM69_INTERRUPT_PIN, true)
        , m_initialized(false) ,m_telemetryPos(0), telemetryMsec(0){}

    bool loop()
    {
        if (!initialized())
            return false;

        // RECEIVING
        // In this section, we'll check with the RFM69HCW to see
        // if it has received any packets:
        if (receiveDone()) // Got one!
        {
            static unsigned char COPY[sizeof(DATA)];
            memcpy(COPY, DATA, sizeof(COPY));
            auto CopyLen = DATALEN;
            if (ACKRequested())
            {
                sendACK(); // library one doesn't work well with one build. see below
            }
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
void loop() 
{
    static const int SHORTEST_STAYWOKEN_MSEC = 100;
    auto now = millis();
    if (printStatusMsec > 0 && now >= printStatusMsec)
    {
        printStatusMsec = 0;
        printStatus();
    }
    bool canSleep = sleepEnabled && (now > InitialAwakeTime);

    // at wakeup time, these are in priority order
#if USE_LCD > 0 || USE_EXTENDER > 0
    auto intFlags = extenderLcd.getCurrentInterruptMask(); // does NOT clear extender interrupt
    if (intFlags & (1 << ExtenderSupport::PD))
        OnPowerDown(); //powerdown interrupt handler does not return
#endif
    // radio wants an ACK in 30msec, although the no-operation loop() measured under 1000 usec
#if USE_RFM69 > 0
    canSleep &= !radio.loop();
#if PRINT_RADIO_RSSI > 0
    {   // radio in an actual hardware build decays RSSI slowly. it takes
        // seconds to go down after a message received.
        // the library sendACK won't send the ack because of that.
        // these prints show the decay
        static long lastprint;
        if (now - lastprint > 1000)
        {
            lastprint = now;
            Serial.print(F("Radio RSSI: ")); Serial.println(radio.readRSSI());
        }
    }
#endif
#endif

    auto buttonMask = readAllButtons(); // clears extender interrupt as a side effect

    static const long BUTTON_DEBOUNCE_MSEC = 100;
    static long lastButtonOnMsec;
    
    // debounce switch read
    static uint8_t dispatched = 0; // only dispatch a button press once
    if (buttonMask == 0)
    {   // don't see any buttons now
        if (now - lastButtonOnMsec > BUTTON_DEBOUNCE_MSEC)
            dispatched = 0; // and only after there has been no button for 20msec
    }
    else
    {
        static const long REPEAT_MSEC = 110;
        int numButtonsPressed = 0;
        // repeating for button held down only works for a single button. 
        auto mask = buttonMask | dispatched;
        for (int i = 0; i < 8; i++)
            if ((mask & (1 << i)) != 0)
                numButtonsPressed += 1;
        if ((buttonMask > dispatched) || // single button repeats
            (numButtonsPressed == 1 && (now - lastButtonOnMsec > REPEAT_MSEC)))
        {
            // for multi-button presses
            if (buttonMask >= 1u << (uint8_t)FrontPanelButtons::DISPATCH_MODE)
                OnModeButton(buttonMask);
            else if (buttonMask >= 1u << (uint8_t)FrontPanelButtons::DISPATCH_ANT)
                OnAntButton(buttonMask);
            else if (buttonMask >= 1u << (uint8_t)FrontPanelButtons::DISPATCH_CDOWN)
                OnCDownButton(buttonMask);
#if USE_LCD > 0 || USE_EXTENDER > 0
            else if (buttonMask >= 1u << (uint8_t)FrontPanelButtons::DISPATCH_CUP)
                OnCUpButton(buttonMask);
            else if (buttonMask >= 1u << (uint8_t)FrontPanelButtons::DISPATCH_LUP)
                OnLUpButton(buttonMask);
            else if (buttonMask >= 1u << (uint8_t)FrontPanelButtons::DISPATCH_LDOWN)
                OnLDownButton(buttonMask);
            else if (buttonMask >= 1u << (uint8_t)FrontPanelButtons::DISPATCH_TUNE)
                OnTuneButton(buttonMask);
#endif
            dispatched = buttonMask;
            lastButtonOnMsec = now;
        }
    }

    canSleep &= (buttonMask == 0);

    canSleep &= !buzzer.loop();

    canSleep &= !freqOver4.loop();

    canSleep &= !bridge.loop(now);

    canSleep &= !swrSearch.loop(now);

#if USE_RFM69 > 0
    {
        uint16_t interval = radio.getTelemetryMsec();
        if ((interval!=0) && (now - radio.getLastTelemetryMsec() > interval))
        {
            uint16_t f,r;
            bridge.readPowerX8(f,r);
            radio.sendTelemetryPacket(freqOver4.getFreqRaw(),f,r, 
#if USE_RELAYS > 0
                    relays.getCindex(), relays.getLindex(), 
                    static_cast<uint8_t>(relays.getCapRelayState()));
#else   
                    0,0,0);
#endif
        }
    }
#endif

#if (DO_PRINT_FREQ > 0) && (USE_LCD > 0)
    {   // put the freqOver4 and bridge results on the LCD
        static long lastPrint;
        static const int PRINT_INTERVAL_MSEC = 500;
        if (now - lastPrint > PRINT_INTERVAL_MSEC)
        {
            lastPrint = now;
            extenderLcd.home();
            int w = extenderLcd.print("F:");
            auto freq = freqOver4.getFreqKhz();
            w+= extenderLcd.print(freq);
            w+= extenderLcd.print("K p:");
            uint16_t f,r;
            bridge.readPowerX8(f,r);
            w+= extenderLcd.print(f);
            w+= extenderLcd.print(" ");
            w+= extenderLcd.print(r);
            while (w < LCD_WIDTH)
                w+=extenderLcd.print(" ");
        }
    }
#endif

    // serial port commands
    while (Serial.available() > 0)
    {
        canSleep = false; // incoming characters cancel sleep
        static const unsigned CMDBUFLEN = 64;
        static char cmdbuf[CMDBUFLEN+1];
        static uint16_t eepromMemAddress;
        static uint8_t cmdbuflen;
        auto c = Serial.read();
        if (c == '\r' || c == '\n')
        {
            if (cmdbuflen < 1)
            {
                Serial.println(F("Commands: S,F"));
                continue;
            }

            if (!processCommandString(cmdbuf, cmdbuflen))
            {
                switch (toupper(cmdbuf[0]))
                {
                // commands present whether we debug or not
                case 'S': // radio commands all start with S
                    if (radioConfiguration.ApplyCommand(cmdbuf))
                    {
                        Serial.print(cmdbuf);
                        Serial.println(F(" command accepted for radio"));
                    }
                    break;

                case 'F':
                    {
                        if ((cmdbuflen > 1) && cmdbuf[1] == 'R')
                        {   // reset calibration to unity
                            freqOver4.setCalibration(1 << 15);
                            Serial.println(F("Now reading uncalibrated frequency"));
                            break;
                        }
                        uint16_t actual, displayed;
                        getTwoInts(cmdbuf, cmdbuflen, actual, displayed);
                        if ((actual > 0) && (displayed > 0))
                        {
                            uint32_t result = actual;
                            result <<= 15;
                            result /= displayed;
                            uint16_t calibration = result;
                            freqOver4.setCalibration(calibration);
                            EEPROM.put(Eeprom328pAddr(FREQ_CALI_OFFSET), calibration);

                            Serial.print(F("Calibration = "));
                            Serial.println(calibration, HEX);
                        }
                        else
                            Serial.println(F("F [R] | [<actual> <displayed>]"));
                    }
                    break;

#if SERIAL_DEBUG > 0 
// these commands are here more for reference to how to do stuff
// They were added in order to test certain features and mostly are no longer useful.
                case 'P':
                    {
                        uint16_t f,r;
                        bridge.readPowerX8(f,r);
                        uint16_t swr = bridge.Swr();
                        Serial.print(F("FWD: ")); Serial.print(f);
                        Serial.print(F(" REF: ")); Serial.print(r);
                        Serial.print(F(" TSWR: 0x")); Serial.print(bridge.TriggerSwr(), HEX);
                        Serial.print(F(" SSWR: 0x")); Serial.print(bridge.StopSearchSwr(), HEX);
                        Serial.print(F(" SWR: 0x")); Serial.println(swr,HEX);
                    }
                    break;
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

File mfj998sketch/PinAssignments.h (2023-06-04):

#pragma once
/* The daughterboard plugs into the PIC18F2520 28pin DIP socket on the MFJ998 main board.
** 13 of those 28 are signals wired directly to Arduino pins (see the circuit diagram)
** The Arduino is a 32 pin part (and so has more pin capacity) but not enough to cover
** all of the PIC and also add the desired new functionality. So an MCP23S08 port extender
** on the Arduino's SPI bus helps out. */
namespace { // constants
    const int SPI_CLOCK_PIN = 13; // must match the CPU hardware because sketch uses the SPI library
    const int SPI_MOSI_PIN = 11; // ditto
    const int SPI_MISO_PIN = 12;    // ditto

    // MFJ998 mainboard pins connected to the Arduino
    const int FREQ_DIV4_PIN = 5;
    const int WAKEUP_PIN = 2;
    const int MFJ998_SDA_PIN = SPI_MOSI_PIN;
    const int MFJ998_CLOCK_AND_MODE_PIN = 9;

    // ... LCD display needs 7 pins
    //const int LCD_D4_PIN = on extender;
    //const int LCD_D5_PIN = on extender;
    //const int LCD_D6_PIN = on extender;
    //const int LCD_D7_PIN = on extender;
    const int LCD_RS_PIN = 4;
    const int LCD_RW_PIN = 7;
    const int LCD_E_PIN = 19;

    const int BUZZ_PIN = 18;

    // ... analog inputs
    const int FWD_ANALOG_PIN = A6; // Empirically: analogRead of 248 corresponds to 100W
    const int REF_ANALOG_PIN = A7;

    const int RELAYS_STROBE_PIN = 10; // on main board

    // front panel switches share pins mobo pins defined above
    const int ANT_BUTTON_PIN = LCD_RS_PIN;
    const int MODE_BUTTON_PIN = MFJ998_CLOCK_AND_MODE_PIN;
    const int CDOWN_BUTTON_PIN = LCD_RW_PIN;
    // these four on extender board
    //const int SW3_PIN = BUTTON_CUP;
    //const int SW5_PIN = BUTTON_LUP;
    //const int SW6_PIN = BUTTON_LDOWN;
    //const int SW7_PIN = BUTTON_TUNE;

    // SPI slaves on daughter board
    const int RFM69_SELECT_PIN = 6; // on daughter board
    const int EXTENDER_CS_PIN = 17;
    const int MEM512_SELECT_PIN = 8;    // on daughter board
    const int RFM69_INTERRUPT_PIN = 3;

    // stuff on MFJ998 main board that we ignore
    // const int MFJ998_START_PIN connected but not supported cuz
    //  we don't support the know the rig interfaces
    // const int MFJ998_SCL_PIN is not connected cuz
    //   we don't use the 25LC512 on the main board

    // these two would be hardware PWM, but the arduino pins that can do hardware
    // PWM are used elsewhere. This sketch uses Timer2 to generate interrupts for 
    // software-implemented PWM
    const int MREF_PIN = 14;
    const int MFWD_PIN = 15;

    //EEPROM locations in on-CPU EEPROM
    const int FREQ_CALI_OFFSET = 0; // beyond end of RadioConfiguration
    const int TRIGGER_SWR = FREQ_CALI_OFFSET + 2;
    const int STOP_SEARCH_SWR = TRIGGER_SWR + 2;
    const int MAX_SWITCHING_V_ADC = STOP_SEARCH_SWR + 2;
    const int MIN_SEARCH_V_ADC = MAX_SWITCHING_V_ADC + 2;
    const int EEPROM_MFJ998_USED = MIN_SEARCH_V_ADC + 2;


}

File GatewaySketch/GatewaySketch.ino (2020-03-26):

#include <RFM69.h>      // the wireless transceiver
#include <SPI.h>        // The relay
#include <RadioConfiguration.h>

#define SERIAL_DEBUG 1
/*  See the mfj998sketch for more details.
** This sketch implents a serial to 900MHz gateway for
** two-way communication with the mfj998 sketch.
** 
** It can run on any Arduino hardware that also has support for
**  Serial library
**  EEPROM library
**  RFM69 library. (which in turn requires SPI)
*/

class RadioRFM69 :  public RFM69
{
public:
    RadioRFM69() : RFM69(RF69_SPI_CS, RF69_IRQ_PIN, true)
    {}

    void setup();
    
    bool loop()
    {
        if (receiveDone()) // Got one!
        {
            Serial.print("N="); Serial.print(SENDERID, DEC);
            Serial.print(" R="); Serial.print(RSSI);
            Serial.print(" [");

            // The actual message is contained in the DATA array,
            // and is DATALEN bytes in size:

            for (byte i = 0; i < DATALEN; i++)
                Serial.print((char)DATA[i]);
            Serial.println("]");
            if (ACKRequested())
            {
                sendACK();
#if SERIAL_DEBUG > 0
                Serial.println("ACK sent");
#endif
            }
        }
    }
protected:
};

namespace {
    RadioRFM69 radio;
    RadioConfiguration radioConfiguration;
    const int AM_GATEWAY_NODEID = 1;
    const int HOST_BUFFER_LENGTH = 64;

    bool processHostCommand(const char *pHost, unsigned short count)
    {
        static const char SENDMESSAGETONODE[] = "SendMessageToNode";
        if (strncmp(pHost, SENDMESSAGETONODE, sizeof(SENDMESSAGETONODE) - 1) == 0)
        {	// send a message to a node now.
            pHost += sizeof(SENDMESSAGETONODE) - 1;
            count -= sizeof(SENDMESSAGETONODE);
            if (*pHost++ == ' ')
            {
                unsigned nodeId = 0;
                for (;; pHost++)
                {
                    if (*pHost >= '0' && *pHost <= '9')
                    {
                        nodeId *= 10;
                        nodeId += *pHost - '0';
                        count -= 1;
                    }
                    else
                        break;
                }
                if ((nodeId >= 0) && *pHost++ == ' ')
                {
                    Serial.print(SENDMESSAGETONODE);
                    Serial.print(" ");
                    Serial.print(nodeId, DEC);
                    Serial.flush();
                    bool acked = radio.sendWithRetry(nodeId, pHost, --count);
#if SERIAL_DEBUG > 0
                    Serial.println(acked? " ACK" : " NAC");
#endif
                 }
            }
            return true;
        }
        else
            return false;
    }
}

void RadioRFM69::setup()
{
    initialize(
        radioConfiguration.FrequencyBandId(),
        AM_GATEWAY_NODEID,	// we're the gateway. we use a non-programmable nodeId
        radioConfiguration.NetworkId());

    uint32_t freq;
    if (radioConfiguration.FrequencyKHz(freq))
        setFrequency(1000*freq);

    setHighPower(); // Always use this for RFM69HCW
    const char *key = radioConfiguration.EncryptionKey();
    if (radioConfiguration.encrypted())
        encrypt(key);
}

void setup()
{
    Serial.begin(9600);
    Serial.print("MFJ998 Gateway ");
    Serial.print(AM_GATEWAY_NODEID, DEC);
    Serial.print(" on network ");
    Serial.print(radioConfiguration.NetworkId(), DEC);
    const char *key = radioConfiguration.EncryptionKey();
    if (radioConfiguration.encrypted())
    {
        Serial.print(" key ");
        for (unsigned j = 0; j < radioConfiguration.ENCRYPT_KEY_LENGTH; j++)
        {
    	    unsigned c = key[j];
    	    if (isprint(c))
    		    Serial.print((char)c);
    	    else
    	    {
    		    Serial.print("\\");
    		    Serial.print(int(c));
    	    }
        }
    }
    radio.setup();
    Serial.print(" Radio on ");
    Serial.print(radio.getFrequency() / 1000);
    Serial.println(" KHz");
    Serial.println(" ready");
}

void loop()
{
    static char fromHostbuffer[HOST_BUFFER_LENGTH + 1]; // +1 so we can add trailing null
    static int charsInBuf = 0;

    while (Serial.available() > 0)
    {
        char input = Serial.read();
        bool isRet = (input == (char)'\r') || (input == (char)'\n');
        if (!isRet) 
        {
            fromHostbuffer[charsInBuf] = input;
            charsInBuf++;
        }

        // If the input is a carriage return, or the buffer is full:
        if (isRet || (charsInBuf == sizeof(fromHostbuffer) - 1)) // CR or buffer full
        {
            fromHostbuffer[charsInBuf] = 0;
            if (radioConfiguration.ApplyCommand(fromHostbuffer))
            {
                Serial.print(fromHostbuffer);
                Serial.println(" command accepted for radio");
            }
            else if (processHostCommand(fromHostbuffer, charsInBuf))
            {
            }
            else
                Serial.println("Invalid command");
            charsInBuf = 0; // reset the packet
        }
    }

    radio.loop();
}

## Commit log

2020-03-26 as built, PCB rev 2
    [Mfj998-db.SLDASM, Mfj998DaughterboardPCBmodel.SLDPRT, Mfj998DaughterboardPCBspacer.SLDPRT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]
2020-03-26 Rev 3 PCB
2020-10-22 control Z0 and account for inductive antenna
2020-10-23 correctly filter gateway messages by nodeid
2020-11-14 power meter can prevent sleep
    [mfj998sketch.ino]
2020-12-23 print startup reliably
2021-11-19 arduino libraries to submodule
2022-11-05 resize behavior for desktop
    [W5XD-loop.ods]
2023-06-04 eeprom settings for power OK to switch/search
